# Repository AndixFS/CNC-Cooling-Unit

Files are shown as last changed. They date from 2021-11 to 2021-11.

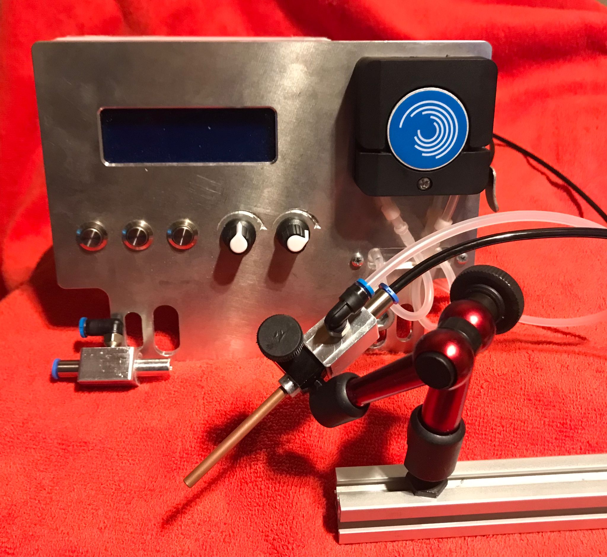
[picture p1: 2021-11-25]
images/Unit.jpg

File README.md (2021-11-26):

# CNC-Cooling-Unit
Minimum quantity lubrication

This is a parts list and some schematics for a CNC cooling unit based on the Pico Pi designed by [Andi FS](https://www.facebook.com/profile.php?id=100017118457747 "Andi FS") posted in the [Home Built CNC Router Projects](https://www.facebook.com/groups/HomeBuiltCNCRouterProjects "Home Built CNC Router Projects") group on Facebook. 

Please feel free to commit changes and help improving the design. Just before commercial use reach out to  [Andi FS](https://www.facebook.com/profile.php?id=100017118457747 "Andi FS")

## Features

This small programm was assembled with a pico pi example for i2c LCD.
Following functions are added
- PWM for a stepper with 50/50 duty cycle and variable frequency 
- ADC for potentiometers
- GPIO for buttons (recognition of pushed, released and hold)
- actual control program

The unit have following functions:
- Pump with the given speed (via poti)
- Boost to fill the hose, boost time via poti
- control 2 valves: air and lubricant
- cooling only with air

I also include plans for hardware (DXF) and a part list. 

### Partlist for CNC cooling unit

| Amount | Part (mechanical)  | Link Germany | Links International |
|--- | --- | ---| --- |
| 1x | Aluminium sheet for front panel 195x150x6mm  | ||  
| 1x | Aluminium for cooling head, 40x15x15 mm  | ||
| 1x | PE 129x109x40mm (for the housing)  | ||
| 3x | 12mm button  | https://www.ebay.de/itm/264492799391 | |
| 1x | Pump  |  https://www.ebay.de/itm/392317740630  | |
| 1x | arm with central clamping |  https://www.ebay.de/itm/143450105517|  | 
| 4x | push fittings for cooling head and pipe adapter, which fits your hoses |  |  |
| 12x | M3x5mm screw (modules)  |  |  |
| 4x | M2x5mm screw (Pico Pi) |  |  | 
| 4x |  M3x45mm screw (housing) |  |  | 
| 4x | M3x12mm screw (LCD) |  |  | 
| 6x | M3x10mm screw (4x pump, 2x hose adapter) |  |  | 
| 150mm | silicone hose OD=4mm ID=2mm (pump to adaper) |  |  | | 

| Amount | Part (Electronics) | Link Germany | Links International |
| --- | --- | --- | --- |
| 2x  | 10k Ohm potentiometer  ||
| 1x | PICO PI  ||
| 1x | 2 channel photocoupler | https://www.ebay.de/itm/284102542027?var=585594324600 |
| 1x |2 channel relais with photocouplers | https://www.ebay.de/itm/353149014364 |
| 1x | Step down power module  | https://www.ebay.de/itm/183980973810 |
| 1x|  Stepper driver carrier board |  https://www.ebay.de/itm/264416015422 |
| 1x  |  Stepper driver A4988  |  https://www.ebay.de/itm/264416015422 |
| 1x |  LCD Module 4x20 | https://www.ebay.de/itm/162451779646 |

### To DO
- Add International Links
- Add Assembly instructions

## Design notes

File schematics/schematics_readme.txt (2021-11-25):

Until I'm able to draw the schematics, here is the PICO PI pinout:
(Note I use the GP and NOT the PIN numbers)
GP0
GP1
GP2
GP3
GP4 LCD SDA 
GP5 LCD SCL
GP6 Relais AIR
GP7 Relais Liquid
GP8
GP9
GP10 Stepper DIR
GP11 Stepper Step
GP12 Opto coupler 1 starting the program 
GP13 Opto coupler 2 no function yet
GP14
GP15
GP16
GP17
GP18 Button 1 - Manual Boost
GP19 Button 2 - Toggle Air only mode
GP20 Button 3 - Togle Auto Boost
GP21
GP22
GP23
GP24
GP25
GP26 ADC Liquid
GP27 ADC Boost Time
GP28
ADC-Ref:
3V3
VSYS
VBUS

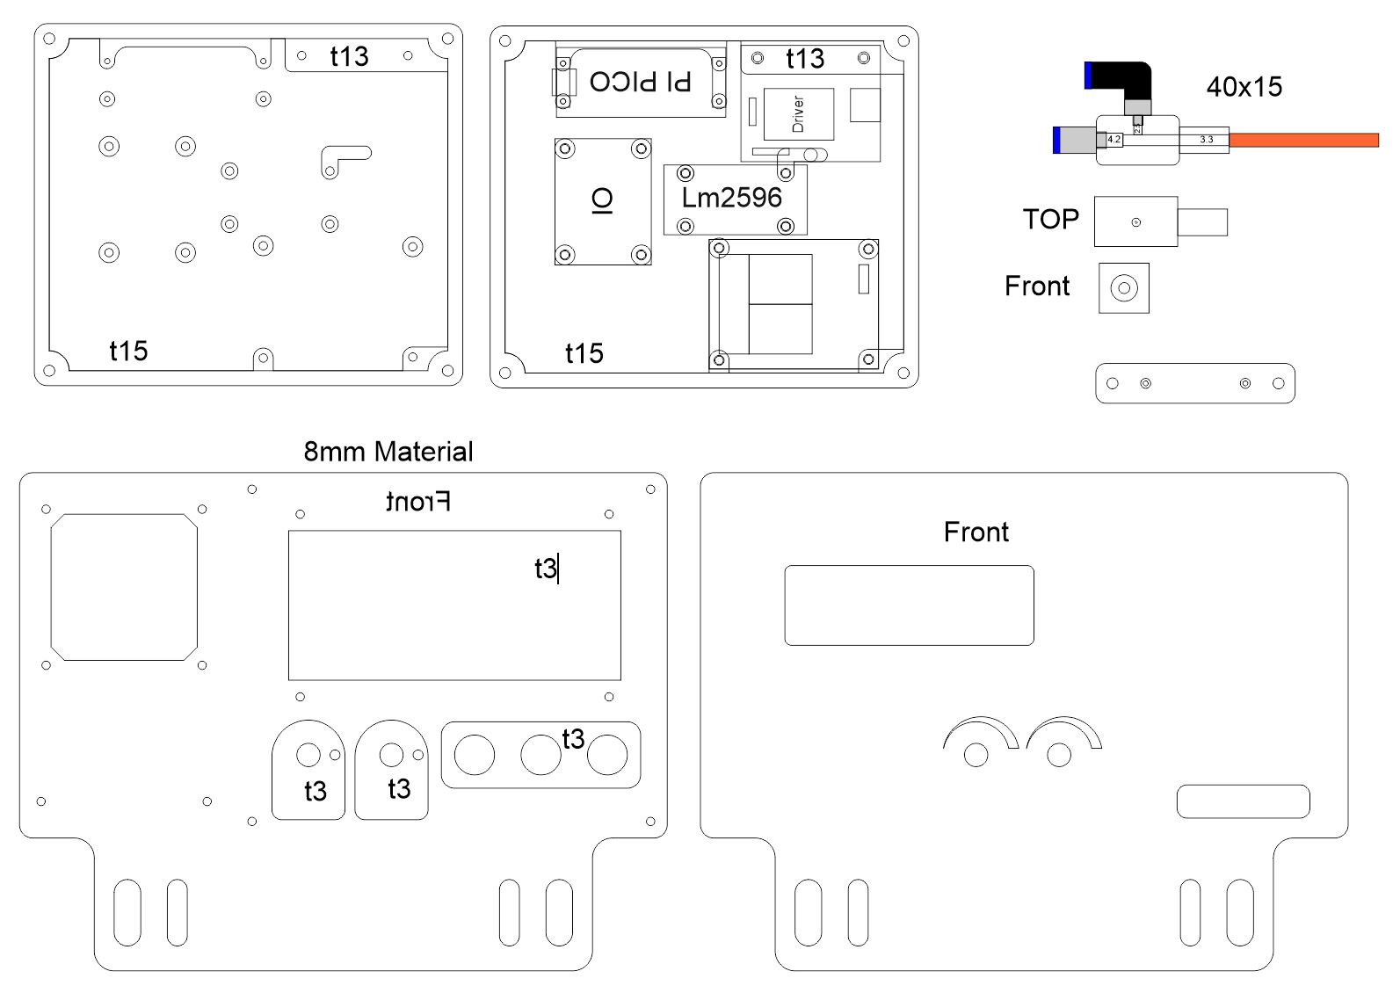
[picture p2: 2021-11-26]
images/Cooling unit front panel and housing.JPG

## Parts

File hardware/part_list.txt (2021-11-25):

Partlist for CNC
- Aluminium sheet for front panel 195x150x6mm
- Aluminium for cooling head, 40x15x15 mm 
- PE 129x109x40mm (for the housing)

Electronics:
- 3pcs 12mm button https://www.ebay.de/itm/264492799391
- 2pcs 10k Ohm potentiometer
- 1pcs PICO PI
- 1pcs 2 channel photocoupler https://www.ebay.de/itm/284102542027?var=585594324600
- 1pcs 2 channel relais with photocouplers https://www.ebay.de/itm/353149014364
- 1pcs Step down power module https://www.ebay.de/itm/183980973810   
- 1pcs Stepper driver carrier board https://www.ebay.de/itm/264416015422
- 1pcs Stepper driver A4988 https://www.ebay.de/itm/264416015422
- 1pcs LCD Module 4x20 https://www.ebay.de/itm/162451779646
- 1pcs Pump https://www.ebay.de/itm/392317740630

Mechanics:
- 1pcs arm with central clamping https://www.ebay.de/itm/143450105517
- 4pcs push fittings for cooling head and pipe adapter, which fits your hoses
- 12pcs M3x5mm screw (modules)
- 4pcs M2x5mm screw (Pico Pi)
- 4pcs M3x45mm screw (housing)
- 4pcs M3x12mm screw (LCD)
- 6pcs M3x10mm screw (4x pump, 2x hose adapter)
- 150mm silicone hose OD=4mm ID=2mm (pump to adaper)

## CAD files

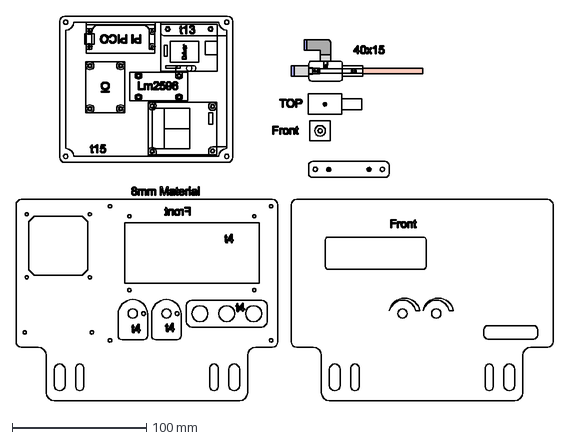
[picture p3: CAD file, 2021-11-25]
hardware/CNC-cooling-unit.dxf
400.0 x 286.6 mm

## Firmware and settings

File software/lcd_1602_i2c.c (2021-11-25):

/**
 * Copyright (c) 2020 Raspberry Pi (Trading) Ltd.
 *
 * SPDX-License-Identifier: BSD-3-Clause
 */

#include <stdio.h>
#include <string.h>
#include "pico/stdlib.h"
#include "hardware/i2c.h"
#include "pico/binary_info.h"
#include "hardware/adc.h"
#include "hardware/pwm.h"
#include "hardware/gpio.h"
#include "hardware/clocks.h"

/* Example code to drive a LCD panel via a I2C bridge chip (e.g. PCF8574)

   GPIO 4 (pin 6)-> SDA on LCD bridge board
   GPIO 5 (pin 7)-> SCL on LCD bridge board
   3.3v (pin 36) -> VCC on LCD bridge board
   GND (pin 38)  -> GND on LCD bridge board
*/
// commands
const int LCD_CLEARDISPLAY = 0x01;
const int LCD_RETURNHOME = 0x02;
const int LCD_ENTRYMODESET = 0x04;
const int LCD_DISPLAYCONTROL = 0x08;
const int LCD_CURSORSHIFT = 0x10;
const int LCD_FUNCTIONSET = 0x20;
const int LCD_SETCGRAMADDR = 0x40;
const int LCD_SETDDRAMADDR = 0x80;

// flags for display entry mode
const int LCD_ENTRYSHIFTINCREMENT = 0x01;
const int LCD_ENTRYLEFT = 0x02;

// flags for display and cursor control
const int LCD_BLINKON = 0x01;
const int LCD_CURSORON = 0x02;
const int LCD_DISPLAYON = 0x04;

// flags for display and cursor shift
const int LCD_MOVERIGHT = 0x04;
const int LCD_DISPLAYMOVE = 0x08;

// flags for function set
const int LCD_5x10DOTS = 0x04;
const int LCD_2LINE = 0x08;
const int LCD_8BITMODE = 0x10;

// flag for backlight control
const int LCD_BACKLIGHT = 0x08;

const int LCD_ENABLE_BIT = 0x04;

// By default these LCD display drivers are on bus address 0x27
static int addr = 0x27;

// Modes for lcd_send_byte
#define LCD_CHARACTER  1
#define LCD_COMMAND    0


#define MAX_LINES      4 
#define MAX_CHARS      20

/* Quick helper function for single byte transfers */
void i2c_write_byte(uint8_t val) {
#ifdef i2c_default
    i2c_write_blocking(i2c_default, addr, &val, 1, false);
#endif
}

void lcd_toggle_enable(uint8_t val) {
    // Toggle enable pin on LCD display
    // We cannot do this too quickly or things don't work
#define DELAY_US 600
    sleep_us(DELAY_US);
    i2c_write_byte(val | LCD_ENABLE_BIT);
    sleep_us(DELAY_US);
    i2c_write_byte(val & ~LCD_ENABLE_BIT);
    sleep_us(DELAY_US);
}

// The display is sent a byte as two separate nibble transfers
void lcd_send_byte(uint8_t val, int mode) {
    uint8_t high = mode | (val & 0xF0) | LCD_BACKLIGHT;
    uint8_t low = mode | ((val << 4) & 0xF0) | LCD_BACKLIGHT;

    i2c_write_byte(high);
    lcd_toggle_enable(high);
    i2c_write_byte(low);
    lcd_toggle_enable(low);
}

void lcd_clear(void) {
    lcd_send_byte(LCD_CLEARDISPLAY, LCD_COMMAND);
}

// go to location on LCD
void lcd_set_cursor(int line, int position) {
    //int val = (line == 0) ? 0x80 + position : 0xC0 + position;
    //int row_offs[]={0x00, 0x40, 0x14, 0x54};
    //int dramaddr = 0x80;
    int val;
    switch(line) {
	case 0:	val = 0x80 + position;
	case 1: val = 0xC0 + position;
	case 2: val = 0x94 + position;
	case 3: val = 0xD4 + position;
    
	default: val = 0x94 + position; 
	}

    lcd_send_byte(val, LCD_COMMAND);
}

static void inline lcd_char(char val) {
    lcd_send_byte(val, LCD_CHARACTER);
}

void lcd_string(const char *s) {
    while (*s) {
        lcd_char(*s++);
    }
}

void lcd_init() {
    lcd_send_byte(0x03, LCD_COMMAND);
    lcd_send_byte(0x03, LCD_COMMAND);
    lcd_send_byte(0x03, LCD_COMMAND);
    lcd_send_byte(0x02, LCD_COMMAND);

    lcd_send_byte(LCD_ENTRYMODESET | LCD_ENTRYLEFT, LCD_COMMAND);
    lcd_send_byte(LCD_FUNCTIONSET | LCD_2LINE, LCD_COMMAND);
    lcd_send_byte(LCD_DISPLAYCONTROL | LCD_DISPLAYON, LCD_COMMAND);
    lcd_clear();
}

/*----------PIN Definition--------------------*/
#define SW0 	 19	// Toggle Air only on/off
#define SW1	 18	// Manual Boost
#define SW2	 20	// Toggle Auto Boost on/off

#define OK0	 12	// Start MIST Cooling Program
#define OK1	 13	// 

#define ADC0_PIN 26
#define ADC1_PIN 27
#define ADC0	 0	//define liquid flow
#define ADC1	 1	//define boost time

#define STEP_DIR 11
#define STEP_S	 10

#define REL0	 6	// Relais for Air
#define REL1	 7	// Relais for Liquid

/*---------Stepper Struct----------------------*/
struct stepper{
	uint f_pwm;
	uint f_sys;
	uint duty;
	uint slice_num;
	float divider;
	uint top;
	uint level;
};

/*---------Switch Struct-------------------------*/
struct sw{
	uint pin;
	uint previous;
	uint current;
	bool toggle;
};

void switch_init(struct sw *drv, uint SW){
	gpio_init(SW);
	gpio_set_dir(SW, GPIO_IN);
	gpio_set_pulls(SW,1,0); //Pullup

	drv->pin      = SW;
	drv->previous = 0;
	drv->current  = 0;
	drv->toggle   = false;
}

void switch_update(struct sw *drv){
	//get switch status
	drv->current = !gpio_get(drv->pin); //True when pressed
	
	//rising edge
       	if(drv->current & (!drv->previous)){
		drv->previous = drv->current;
		drv->toggle = !drv->toggle;
	}

	if((!drv->current) & drv->previous){
		drv->previous = drv->current;
	}
}


void stepper_init(struct stepper *drv){
	// init DIR = GPIO 11
	gpio_init(STEP_DIR);
	gpio_set_dir(STEP_DIR, GPIO_OUT); 

	//setup PWM module variables
	drv->f_pwm = 0;
	drv->duty  = 50; //50% Duty cycle
	
	gpio_set_function(STEP_S, GPIO_FUNC_PWM);
	drv->slice_num = pwm_gpio_to_slice_num(STEP_S);
	drv->f_sys = clock_get_hz(clk_sys);
	drv->divider = drv->f_sys / 1000000UL;
	pwm_set_clkdiv(drv->slice_num, drv->divider);


}

void stepper_set_speed(struct stepper *drv, uint speed, bool dir){
	
	//set direction
	gpio_put(STEP_DIR,dir);
	
	//set speed
	drv->top = 1000000UL/speed -1;
	pwm_set_wrap(drv->slice_num, drv->top);
	drv->level = (drv->top+1) * drv->duty / 100 -1; 
	pwm_set_chan_level(drv->slice_num, 0,drv->level);
	pwm_set_enabled(drv->slice_num, true);
}

void stepper_stop(struct stepper *drv){
	
	pwm_set_enabled(drv->slice_num,false);

}

uint steps2ml(uint steps){
	return ((steps*16)/4096);
}


int main() {
	stdio_init_all();
	adc_init();
	adc_gpio_init(ADC0_PIN);
	adc_gpio_init(ADC1_PIN);

#if !defined(i2c_default) || !defined(PICO_DEFAULT_I2C_SDA_PIN) || !defined(PICO_DEFAULT_I2C_SCL_PIN)
    #warning i2c/lcd_1602_i2c example requires a board with I2C pins
#else
    	// This example will use I2C0 on the default SDA and SCL pins (4, 5 on a Pico)
    	i2c_init(i2c_default, 100 * 1000);
    	gpio_set_function(PICO_DEFAULT_I2C_SDA_PIN, GPIO_FUNC_I2C);
    	gpio_set_function(PICO_DEFAULT_I2C_SCL_PIN, GPIO_FUNC_I2C);
    	gpio_pull_up(PICO_DEFAULT_I2C_SDA_PIN);
    	gpio_pull_up(PICO_DEFAULT_I2C_SCL_PIN);
    	// Make the I2C pins available to picotool
    	bi_decl(bi_2pins_with_func(PICO_DEFAULT_I2C_SDA_PIN, PICO_DEFAULT_I2C_SCL_PIN, GPIO_FUNC_I2C));

    	lcd_init();

	struct stepper *pump_ptr, pump;
	pump_ptr = &pump;

	struct sw *sw0_ptr, *sw1_ptr, *sw2_ptr, sw0, sw1, sw2;
	sw0_ptr = &sw0;
	sw1_ptr = &sw1;
	sw2_ptr = &sw2;

	uint adc0_speed;
	uint adc1_time;

	uint boost_time  = 0;
	uint boost_speed = 6500;
	uint lcd_timer   = 30;	
	uint lcd_refresh = 60;  // lcd refresh time (x*prog_time)
	uint prog_time   = 5; //programm cycle time in ms
	uint speed_ml    = 0;

	char lcd0_str[21];
	char lcd1_str[21];
	char lcd2_str[21];
	char lcd3_str[21];

	switch_init(sw0_ptr,SW0);
	sw0.toggle = 1;
	switch_init(sw1_ptr,SW1);
	switch_init(sw2_ptr,SW2);

	//Init optocouplers
	 
	gpio_init(OK0);
	gpio_set_dir(OK0, GPIO_IN);
	gpio_set_pulls(OK0,1,0); //Pullup

	gpio_init(OK1);
	gpio_set_dir(OK1, GPIO_IN);
	gpio_set_pulls(OK1,1,0); //Pullup

	//Init Relais
	gpio_init(REL0);
	gpio_set_dir(REL0, GPIO_OUT); 
	gpio_put(REL0,1); //turn relais off

	gpio_init(REL1);
	gpio_set_dir(REL1, GPIO_OUT); 
	gpio_put(REL1,1); //turn relais off

	stepper_init(pump_ptr);
	stepper_set_speed(pump_ptr,1,0);
	sleep_ms(10);
	stepper_set_speed(pump_ptr,1,1);
	sleep_ms(10);
	stepper_stop(pump_ptr);
	

    while (1) {
	//update switches    
	switch_update(sw0_ptr);
	switch_update(sw1_ptr);
	switch_update(sw2_ptr);
	//measure ADC
	adc_select_input(ADC0);    
	adc0_speed = adc_read()*2;
	speed_ml = steps2ml(adc0_speed);
	adc_select_input(ADC1);
	adc1_time = adc_read()/4;
	
	//Programm start
	// Set Relais
	if(!gpio_get(OK0)){
		gpio_put(REL0,0);
	}
	else{
		gpio_put(REL0,1);
	}	
	
	if((!gpio_get(OK0)) & (sw0.toggle)){
		gpio_put(REL1,0);
	}
	else{
		gpio_put(REL1,1);
	}

	//manual boost
	if(sw1.current){
		adc0_speed = boost_speed;
		speed_ml = steps2ml(boost_speed);
	}

	if((!gpio_get(OK0)) & (sw0.toggle)){
		//is boost activated
		if((boost_time > 0) & (sw2.toggle)){
			stepper_set_speed(pump_ptr, boost_speed, false);
			speed_ml = steps2ml(boost_speed);

			boost_time--;
		}
		else{
			stepper_set_speed(pump_ptr, adc0_speed,false);
		}



	}
	else{
		//set boost time if boost is activeded
		if(sw2.toggle){
			boost_time = adc1_time;
		}
		
		stepper_stop(pump_ptr);

	}
	

//speed_ml
	uint sec  = boost_time*prog_time/500;

	sprintf(lcd0_str,"Flow:   %2d ml/min   ", speed_ml);
	if(sw2.toggle & (gpio_get(OK0)))
		sprintf(lcd1_str,"Boost:  %2d s   activ", sec);
	
	if(sw2.toggle & !(gpio_get(OK0)) & sw0.toggle)
		sprintf(lcd1_str,"Boost:  %2d s left   ", sec);
	

	if(!(sw2.toggle) & (gpio_get(OK0)))
		sprintf(lcd1_str,"Boost:   off        ");



	//sprintf(lcd2_str,"--------------------");
	if (sw0.toggle){
		sprintf(lcd2_str,"Cooling: Mist       ");
	}
	else{
		sprintf(lcd2_str,"Cooling: Air only  ");
	}

	sprintf(lcd3_str,"|Man|Air|Boost|ml|s|");


	//LCD update cycle
	if(lcd_timer <= 0){
		//update display
		//LCD line 0
		lcd_send_byte(0x80,LCD_COMMAND);
		lcd_string(lcd0_str);

		//LCD line 1
		lcd_send_byte(0xC0,LCD_COMMAND);
		lcd_string(lcd1_str);

		//LCD line 2
		lcd_send_byte(0x94,LCD_COMMAND);
		lcd_string(lcd2_str);

		//LCD line 3
		lcd_send_byte(0xD4,LCD_COMMAND);
		lcd_string(lcd3_str);
		
		lcd_timer=lcd_refresh;
	}
	else{
		//decrease timer
		lcd_timer--;
	}

	sleep_ms(prog_time);
        //lcd_clear();


	}
    return 0;
#endif
}

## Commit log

2021-11-25 adding DXF and image
    [CNC-cooling-unit.dxf]
2021-11-26 Add drawing of front panel and housing
2021-11-26 fixt minor failure, depth is only 3mm
